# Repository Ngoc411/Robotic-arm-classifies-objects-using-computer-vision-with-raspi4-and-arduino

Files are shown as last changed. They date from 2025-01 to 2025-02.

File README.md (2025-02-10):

# Robotic-arm-classifies-objects-using-computer-vision-with-raspi4-and-arduino

## Description

This project involves a robotic arm capable of classifying objects using computer vision and sorting them accordingly. A Raspberry Pi 4 processes images captured from a camera, runs a trained machine learning model, and communicates with an Arduino to control the robotic arm’s movements.

<div align="center">
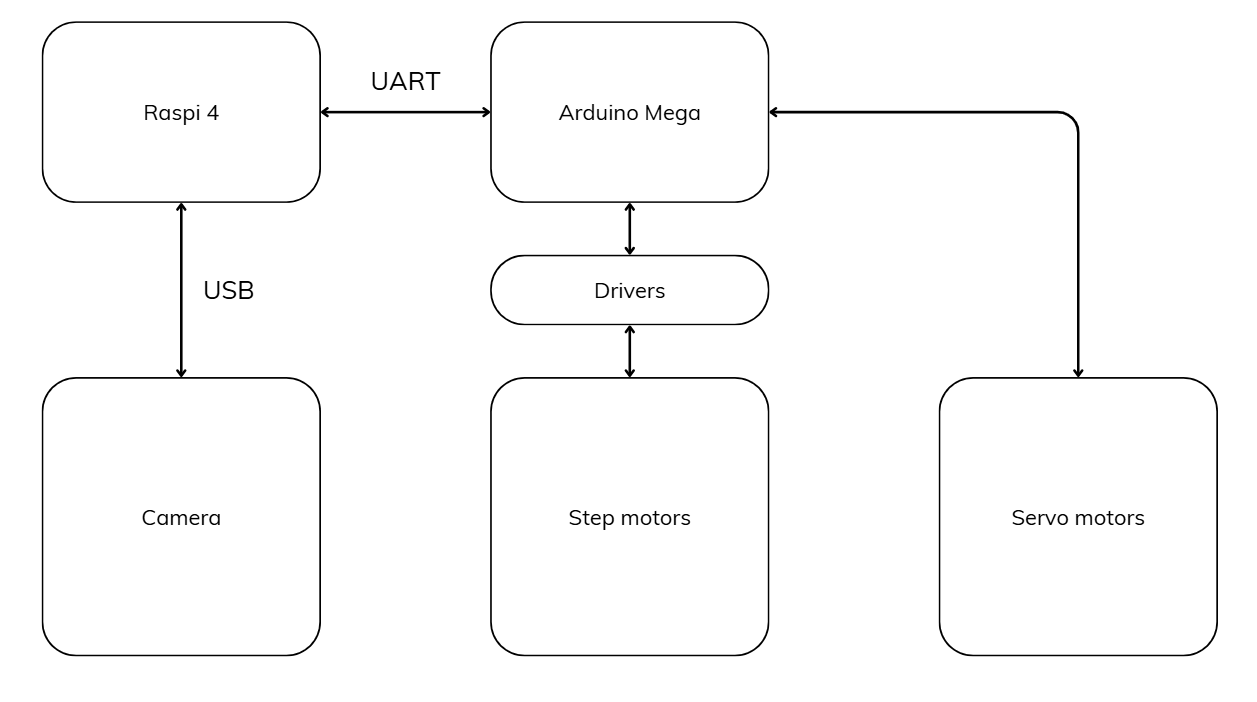
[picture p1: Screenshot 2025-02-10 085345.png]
  
</div>
<div align="center">
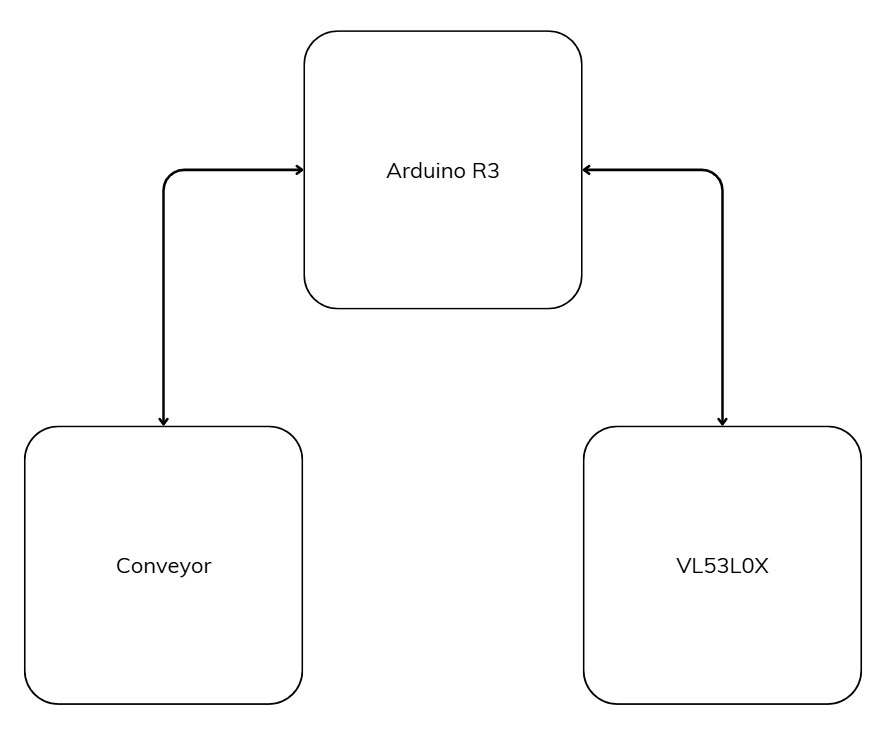
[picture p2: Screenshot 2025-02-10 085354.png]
  
</div>
<div align="center">
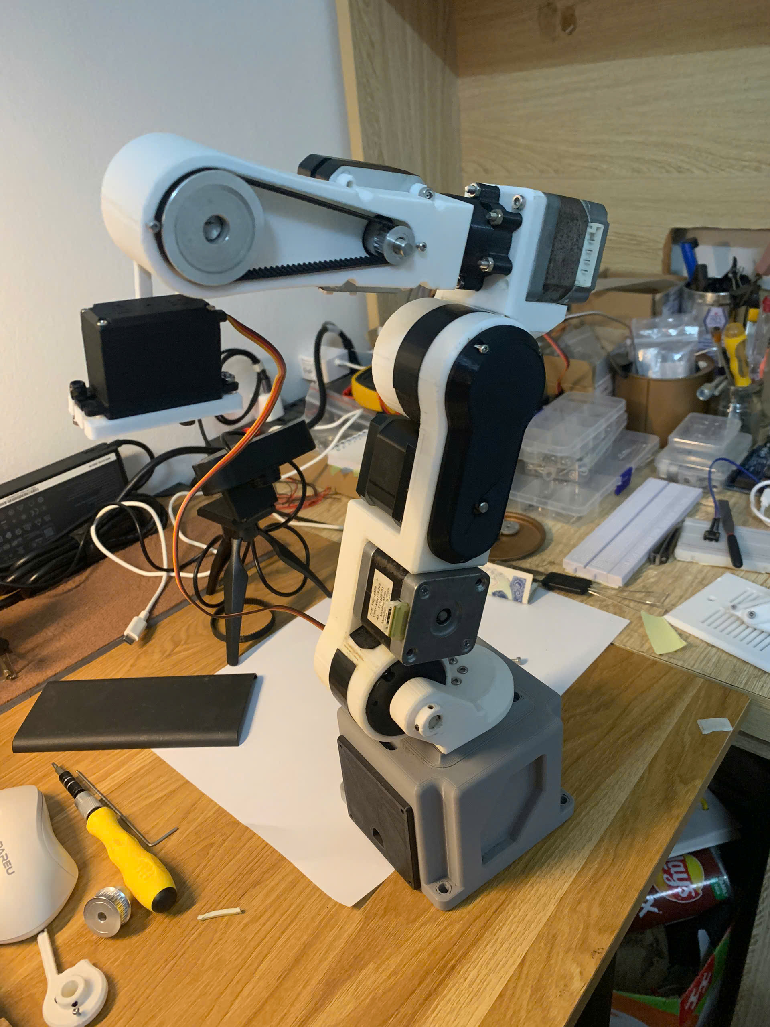
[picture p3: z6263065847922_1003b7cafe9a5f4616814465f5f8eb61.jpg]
  
</div>

## System Overview
1. Computer Vision Subsystem: Identifies and classifies objects

```mermaid
graph TD;
  A(Start) --> B(Initialize Camera & Load Model)
  B --> C(Capture Image)
  C --> D(Preprocess Image)
  D --> E(Run Object Classification Model)
  E -->|Success| F(Identify Object & Determine Target)
  E -->|Failure| C
  F --> G(Convert to Movement Commands)
  G --> H{received_data = True?}
  H -->|No| M{Exit?}
  H -->|Yes| I(Send Command to Arduino)
  I --> J(Set received_data = False)
  J --> K{Wait for Acknowledgment?}
  K -->|No| M
  K -->|Yes| L(Set received_data = True)
  M -->|No| C
  M -->|Yes| N(End)
```
  
2. Robotic Control Subsystem: Moves the robotic arm based on classifications.

``` mermaid
graph TD;
  A(Start) --> B(Initialize Serial Communication & Motors)
  B --> C{Wait for Command?}
  C -->|No| C
  C -->|Yes| D(Decode Received Command)
  D --> E(Convert to Joint Angles)
  E --> F{Are Angles Valid?}
  F -->|No| G(Send Error & Return to Wait)
  F -->|Yes| H(Move Servos)
  H --> I{Movement Complete?}
  I -->|No| H
  I -->|Yes| J(Send Acknowledgment to Raspberry Pi)
  J --> K{Exit?}
  K -->|Yes| C
  K -->|No| L(End)
```

## Hardware Components

- Raspberry Pi 4: Runs object classification and sends movement commands.
- Arduino: Controls the robotic arm servos.
- Camera Module: Captures images for object recognition.
- Robotic Arm with Step Motors and Servo Motors: Moves objects based on classification.
- Drivers: 8825
- Power Supply: 24V 5A Provides power to components.
- Arm design
<div align="center">
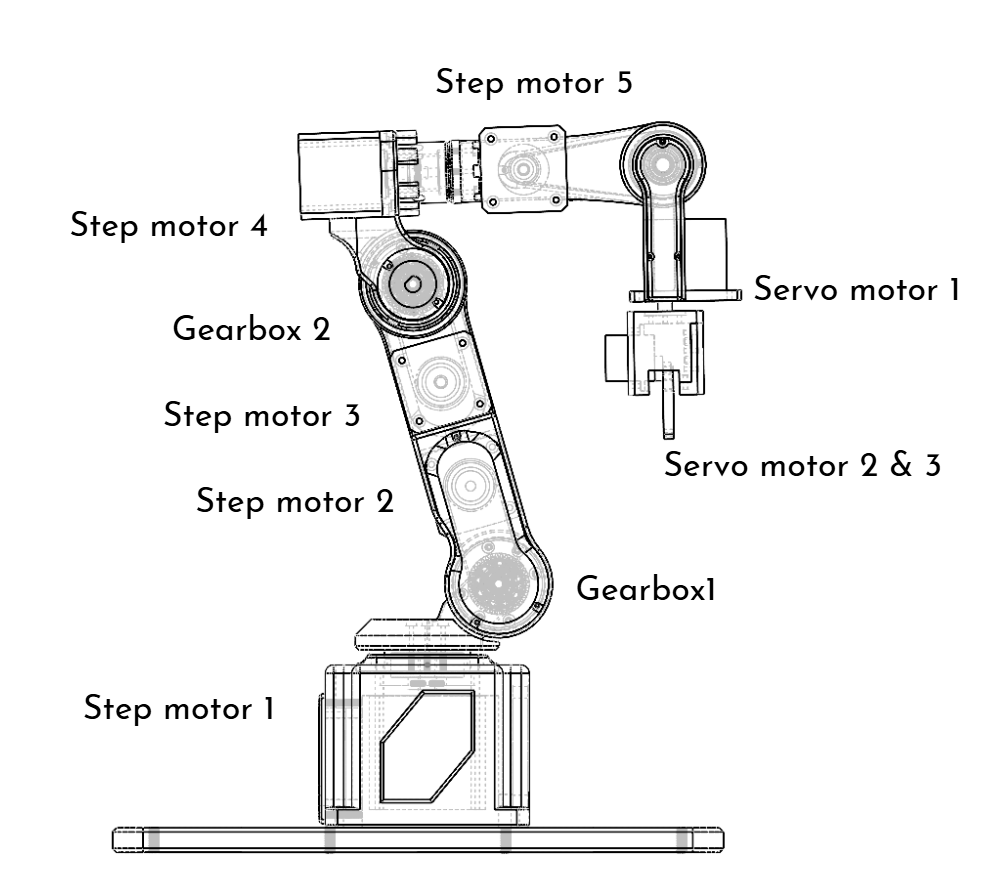
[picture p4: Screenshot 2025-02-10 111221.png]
  
</div>

## Model Training Process

1. Data Collection: Capture images of objects using the camera module.
<div align="center"; display="flex">
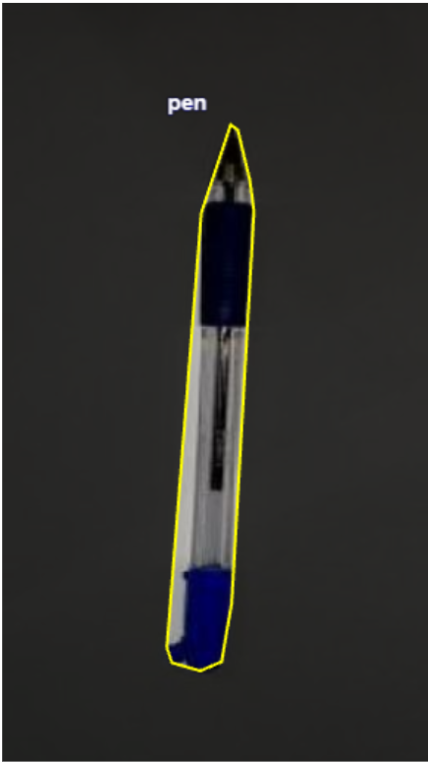
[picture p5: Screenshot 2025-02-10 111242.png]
  
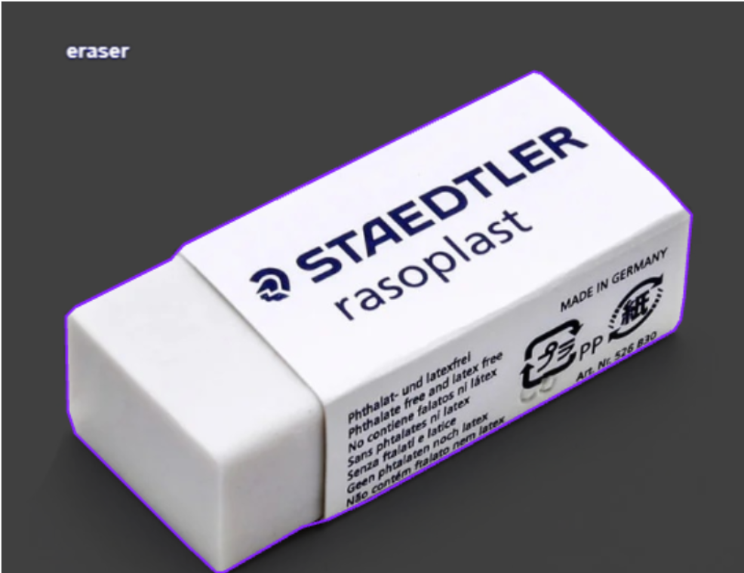
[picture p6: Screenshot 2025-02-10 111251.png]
  
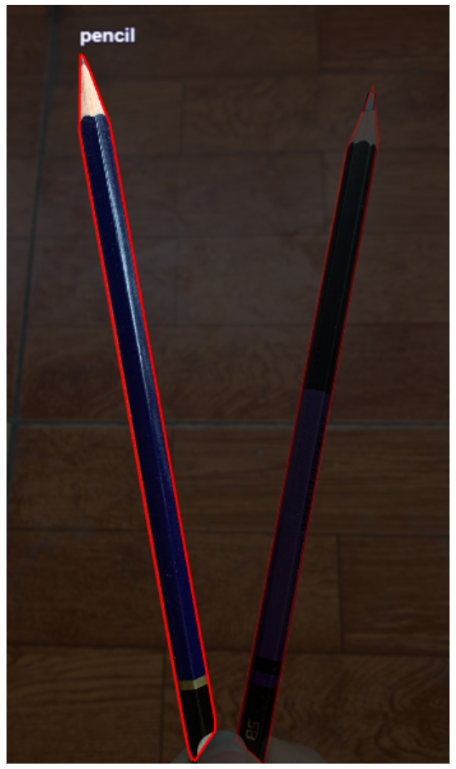
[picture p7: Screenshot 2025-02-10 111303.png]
  
</div>
2. Preprocessing: Resize, normalize, and augment images.

<div align="center">
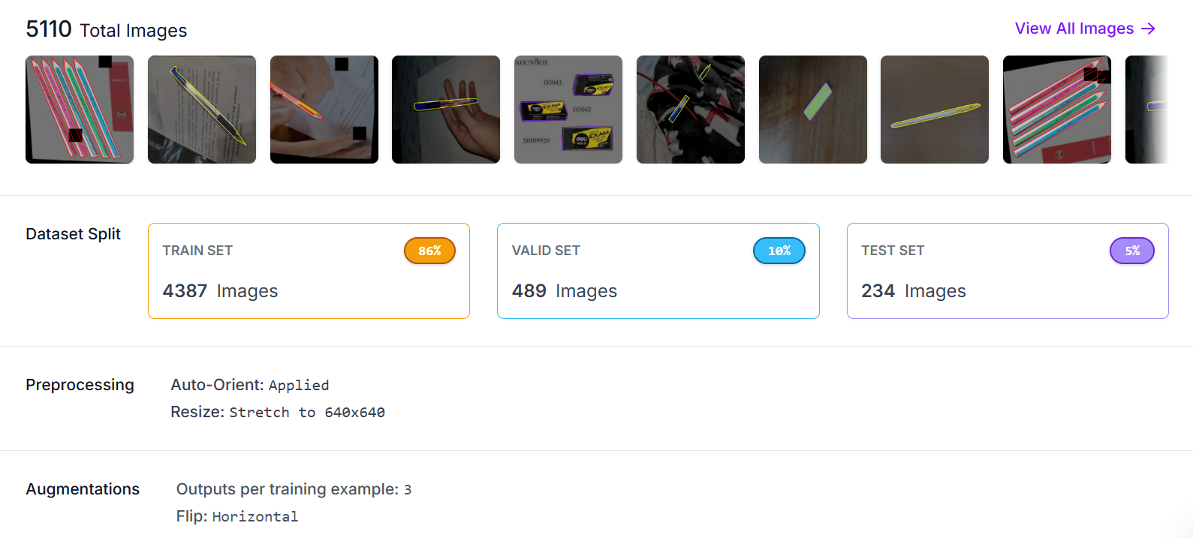
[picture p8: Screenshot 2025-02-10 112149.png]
  
</div>

3. Model Selection: Use a convolutional neural network (CNN) for classification.
4. Training: Train the model using TensorFlow/Keras.

<div align="center"; display="flex">
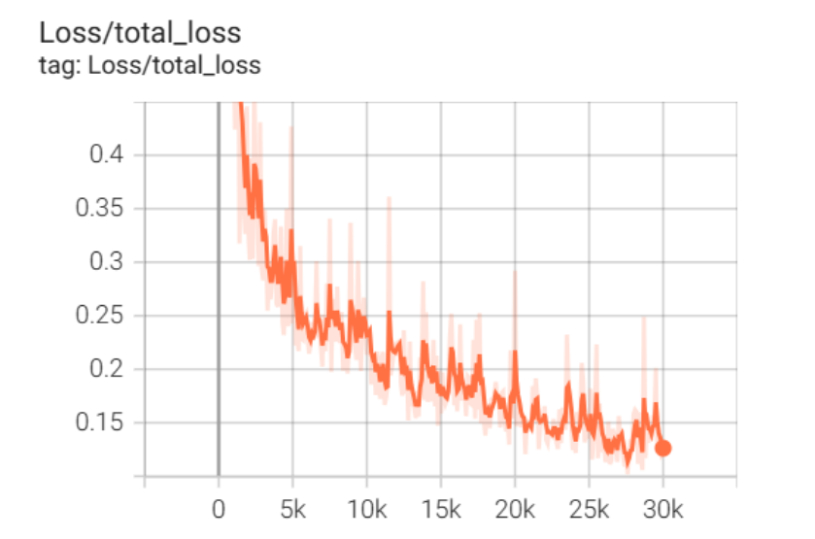
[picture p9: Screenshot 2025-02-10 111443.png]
  
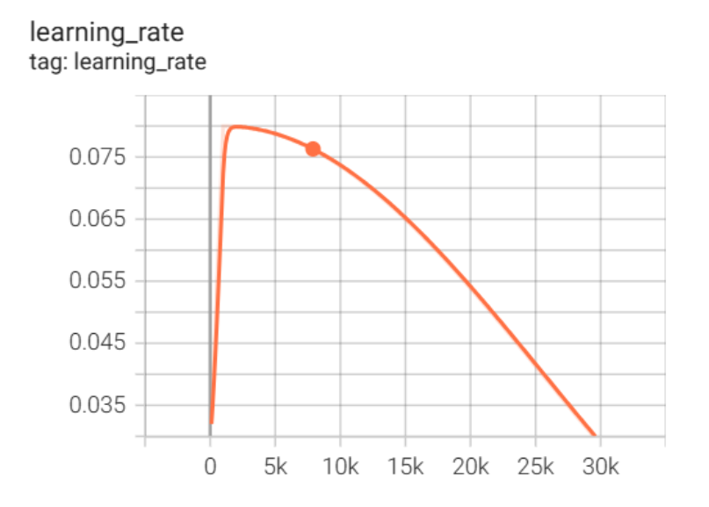
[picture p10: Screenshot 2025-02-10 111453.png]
  
</div>

5. Deployment: Convert the trained model to a format suitable for Raspberry Pi.

## Robotic Arm Kinematics

<div align="center">
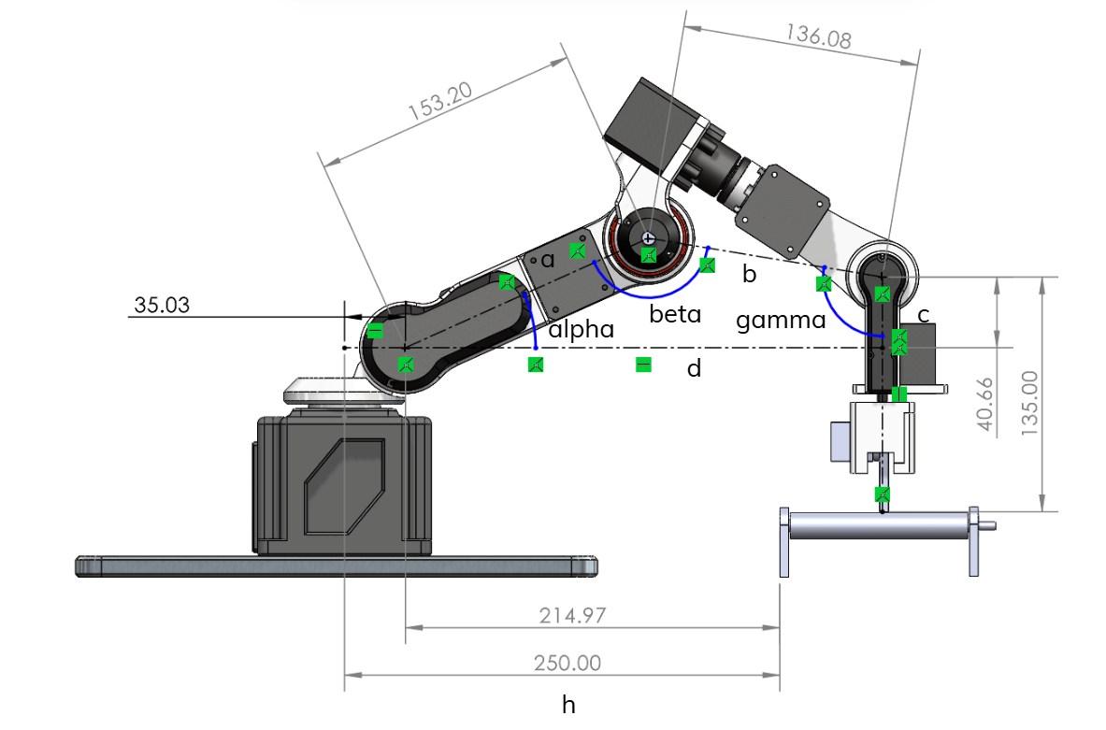
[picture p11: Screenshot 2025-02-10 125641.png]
  
</div>

The problem is to find 3 main angles: alpha, beta and gamma with fixed length a, b, c and h

<div align="center">
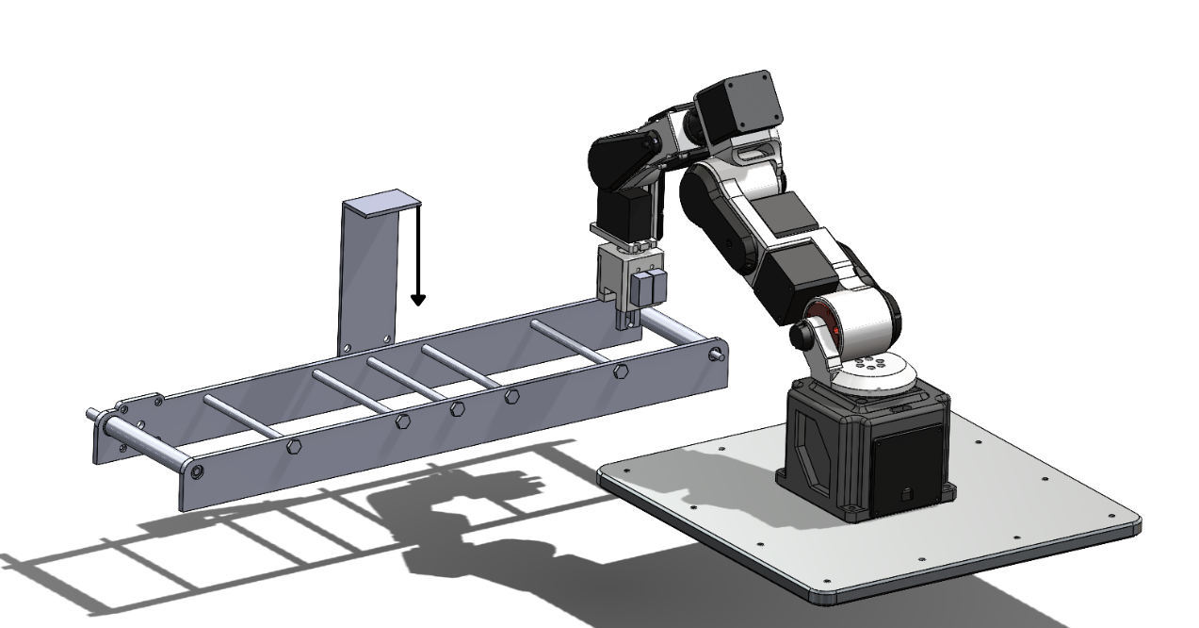
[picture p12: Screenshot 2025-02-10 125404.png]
  
</div>

The camera will be up side down like this, so we can base on the following picture to measure the coordinate of objects

<div align="center">
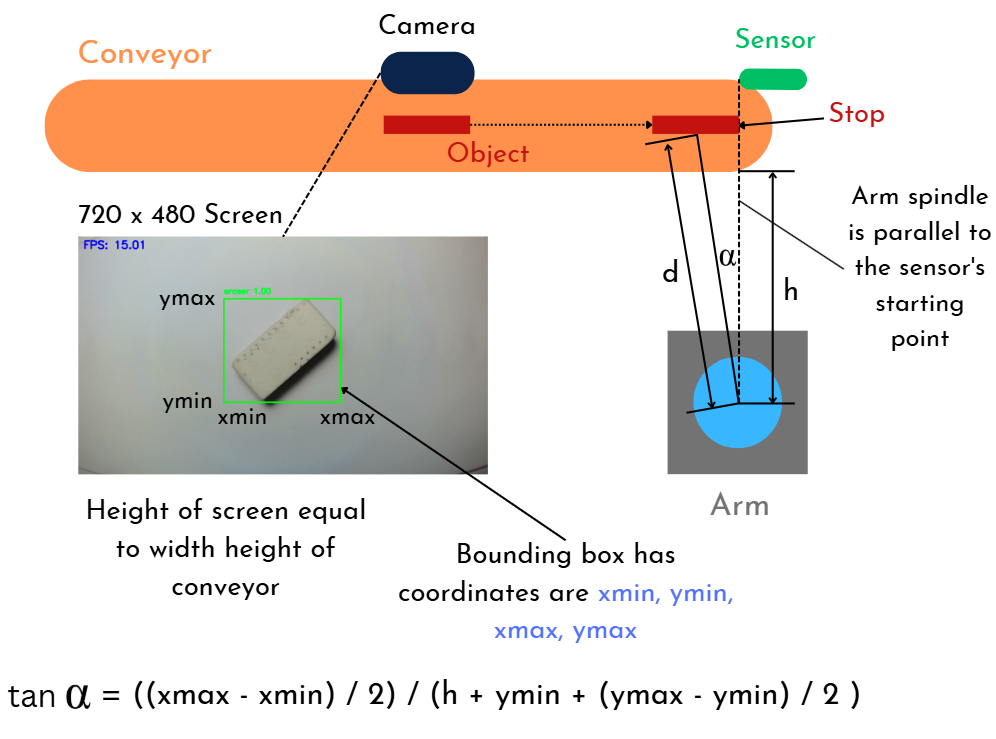
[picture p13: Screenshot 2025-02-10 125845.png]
  
</div>

## Operation

1. System Initialization: Start Raspberry Pi and Arduino.
2. Object Detection: Capture image and classify the object.

<div align="center">
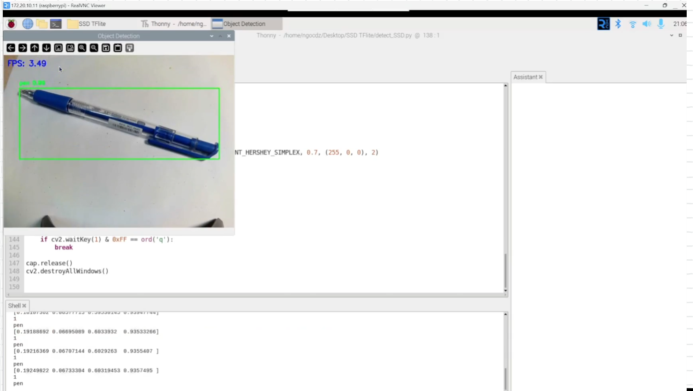
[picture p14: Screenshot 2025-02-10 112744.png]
  
</div>
<div align="center">
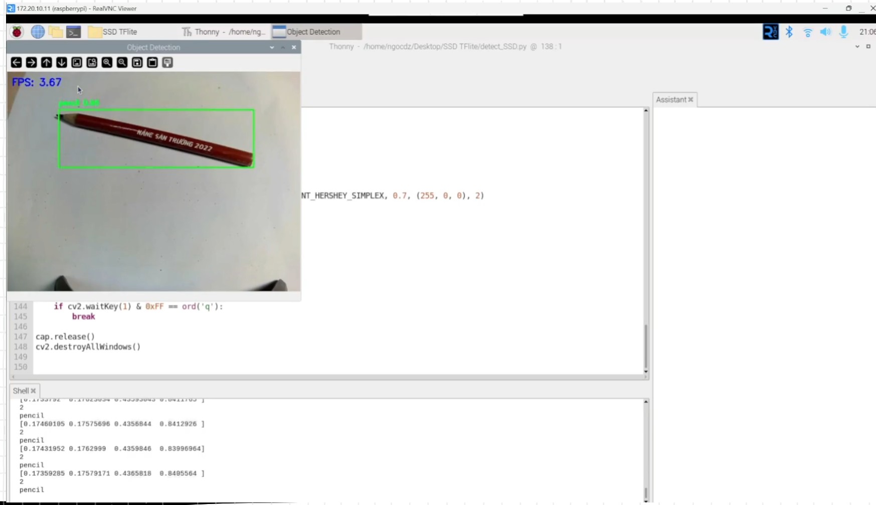
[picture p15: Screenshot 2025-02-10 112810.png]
  
</div>
<div align="center">
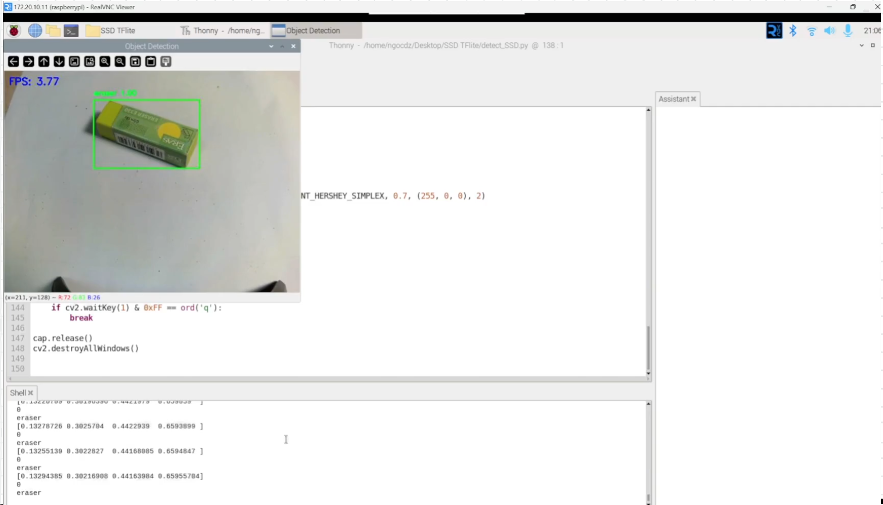
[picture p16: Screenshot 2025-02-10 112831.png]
  
</div>

3. Robotic Arm Movement: Calculate and execute joint angles for object handling.

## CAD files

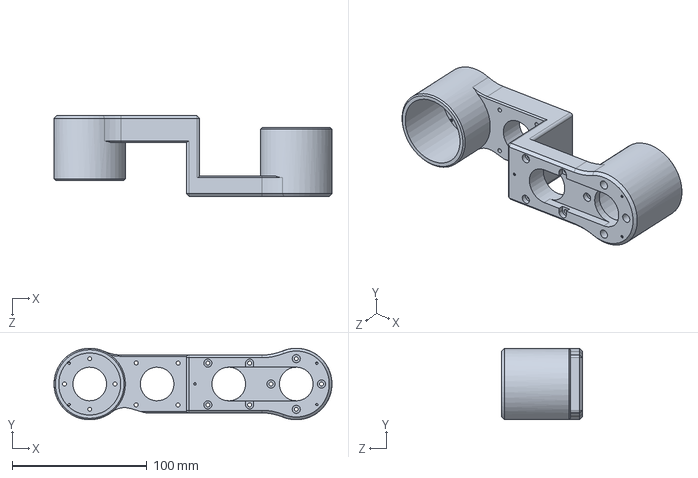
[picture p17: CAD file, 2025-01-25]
SolidW/Arm/Main Arm 1.SLDPRT
206.2 x 53.0 x 60.0 mm

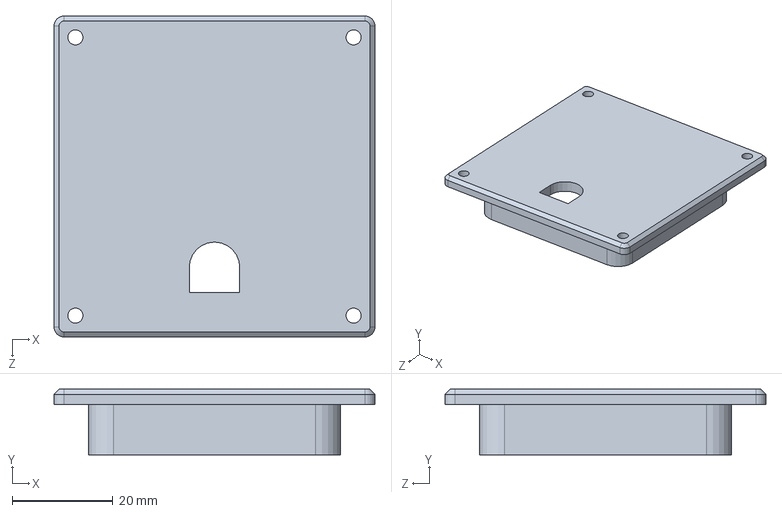
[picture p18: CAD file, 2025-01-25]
SolidW/Case/Part6 - Case.SLDPRT
63.6 x 13.0 x 63.6 mm

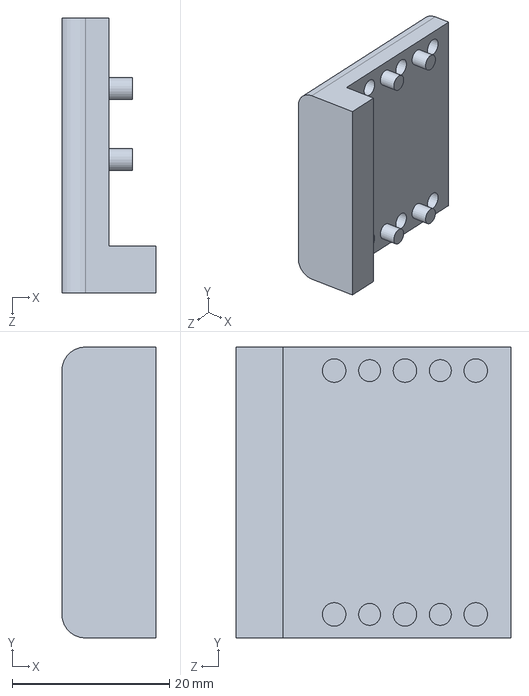
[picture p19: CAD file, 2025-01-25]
SolidW/Hand/Hand - 2.SLDPRT
12.0 x 37.0 x 35.0 mm

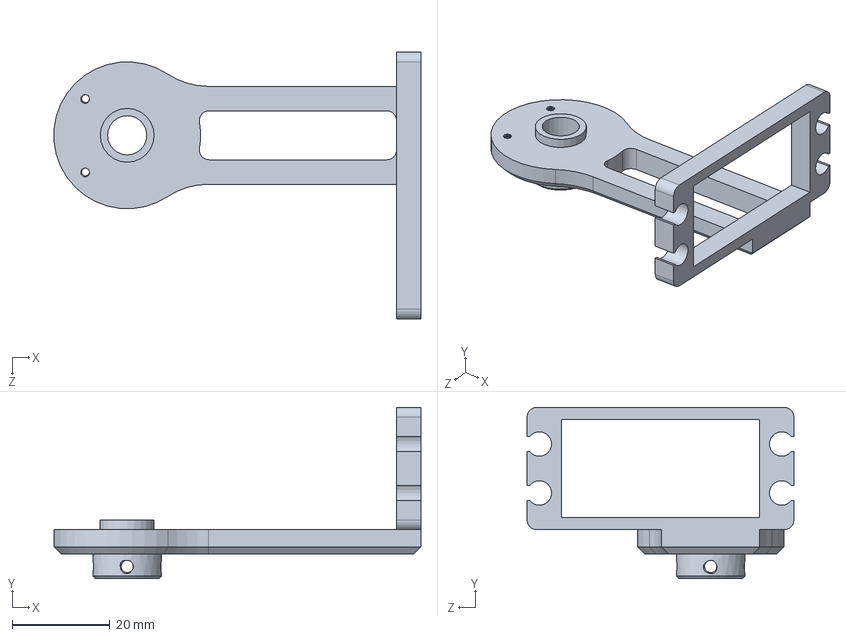
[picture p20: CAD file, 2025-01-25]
SolidW/Arm/Mini Arm.SLDPRT
74.9 x 35.0 x 54.5 mm

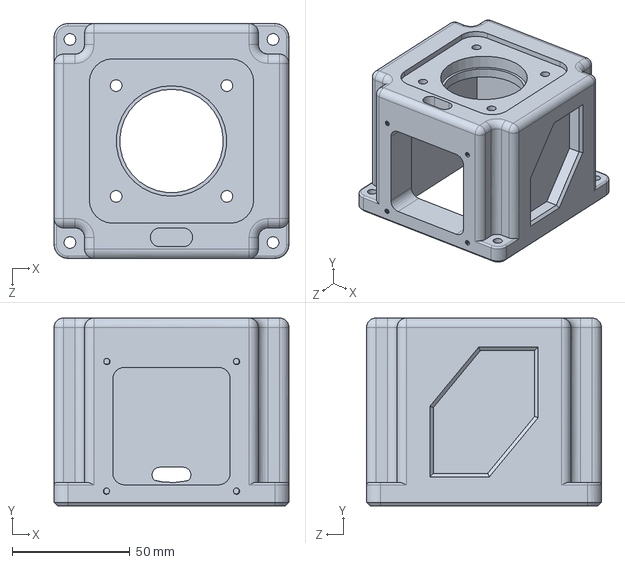
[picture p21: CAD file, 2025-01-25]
SolidW/Base/Base Case.SLDPRT
100.0 x 80.0 x 100.0 mm

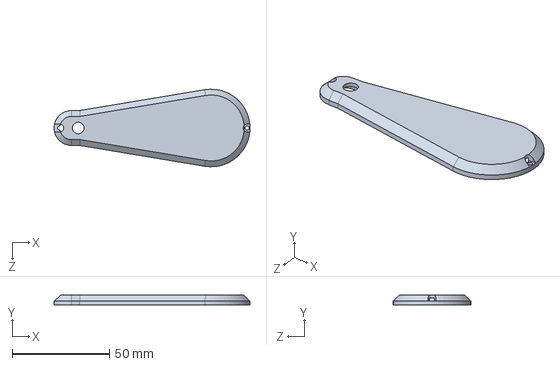
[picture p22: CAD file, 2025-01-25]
SolidW/Case/Part2 - Case.SLDPRT
101.0 x 5.00 x 40.0 mm

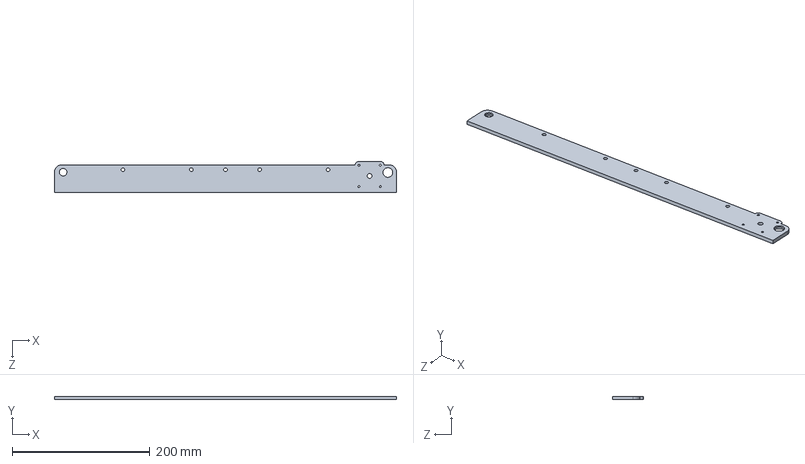
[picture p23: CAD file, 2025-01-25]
SolidW/Conveyor/Part2.SLDPRT
496.0 x 5.00 x 45.0 mm

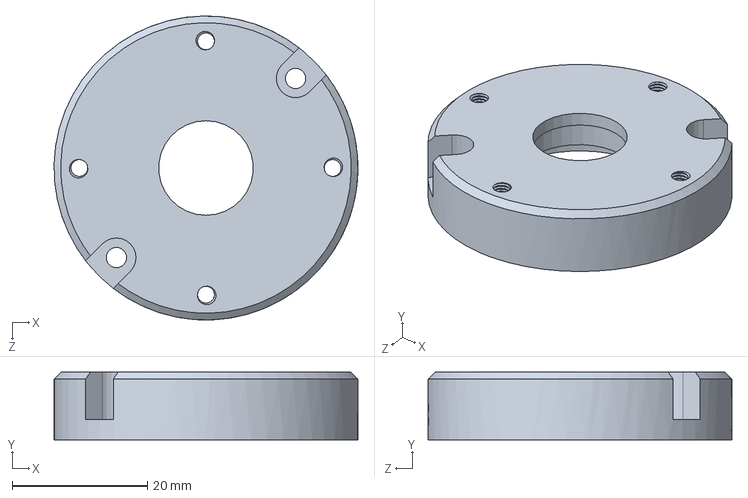
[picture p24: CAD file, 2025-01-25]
SolidW/Gearbox/Case Top.SLDPRT
45.0 x 10.0 x 45.0 mm

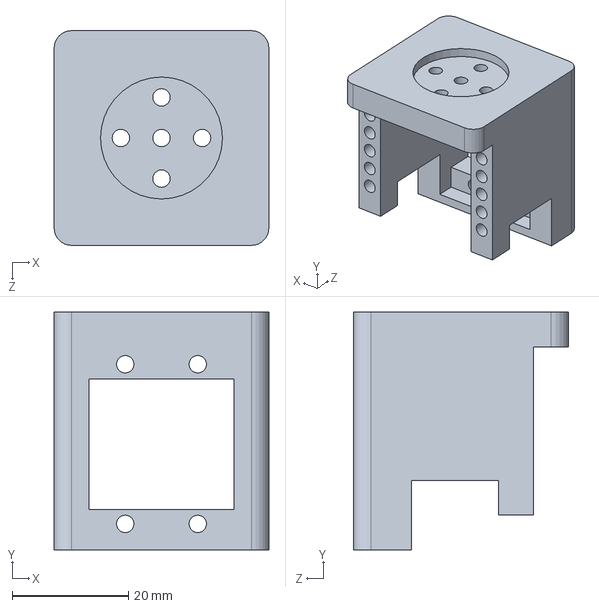
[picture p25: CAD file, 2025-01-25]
SolidW/Hand/Hand - 1.SLDPRT
37.0 x 41.0 x 37.0 mm

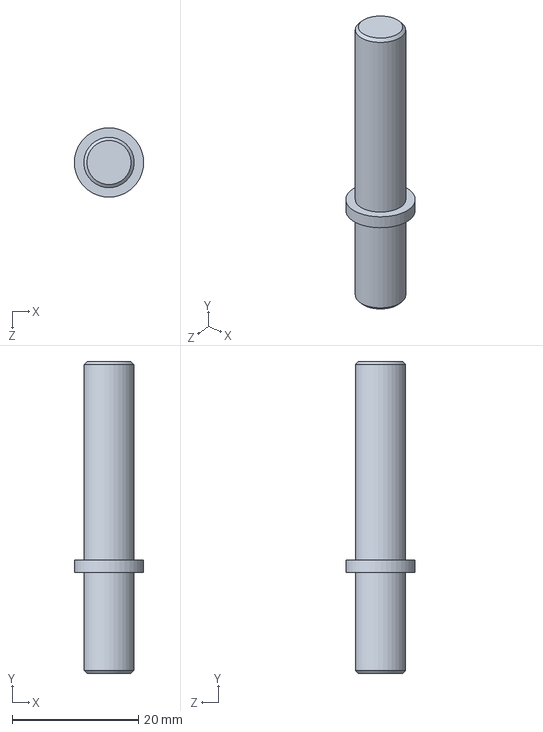
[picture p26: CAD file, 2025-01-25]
SolidW/Arm/Bar Connection Extra Arm 1.SLDPRT
11.0 x 49.5 x 11.0 mm

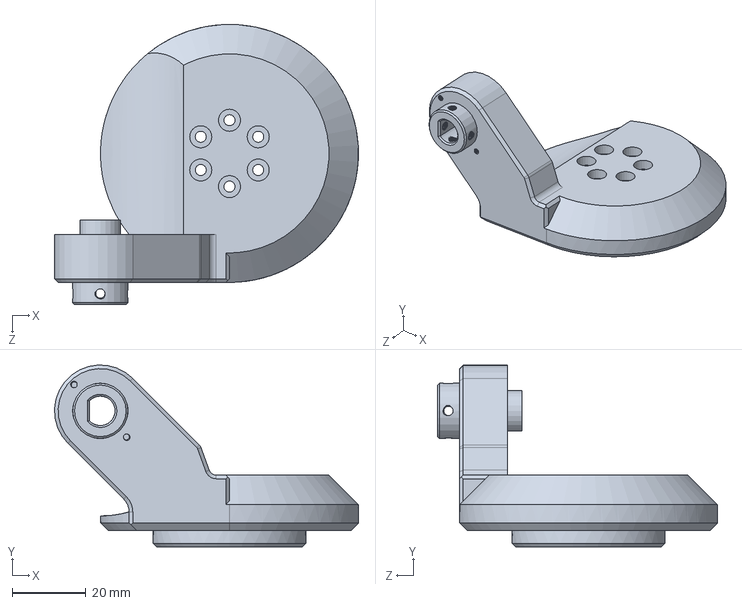
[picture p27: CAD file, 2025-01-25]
SolidW/Base/Base Connection 2.SLDPRT
82.5 x 49.4 x 76.0 mm

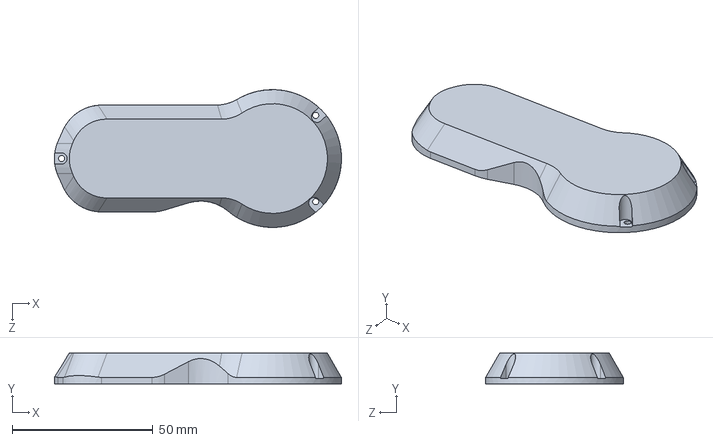
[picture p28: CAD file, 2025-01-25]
SolidW/Case/Part3 - Case.SLDPRT
102.0 x 11.0 x 49.0 mm

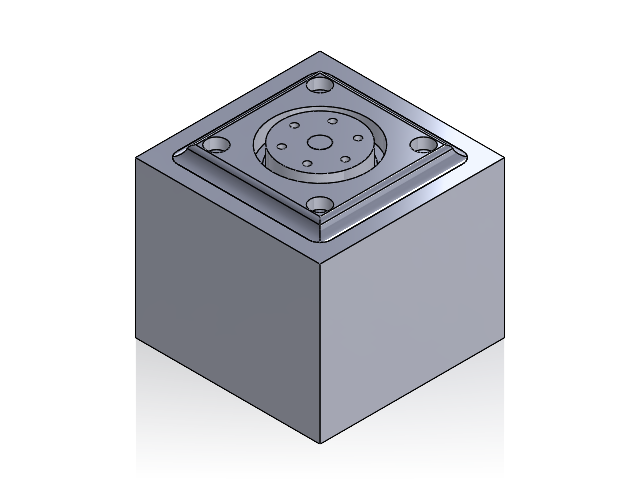
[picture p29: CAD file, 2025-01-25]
SolidW/Base/Assem Base.SLDASM
Base Case
Step Motor 57
Base Connection
Bearing 35x47x7
Bearing Block

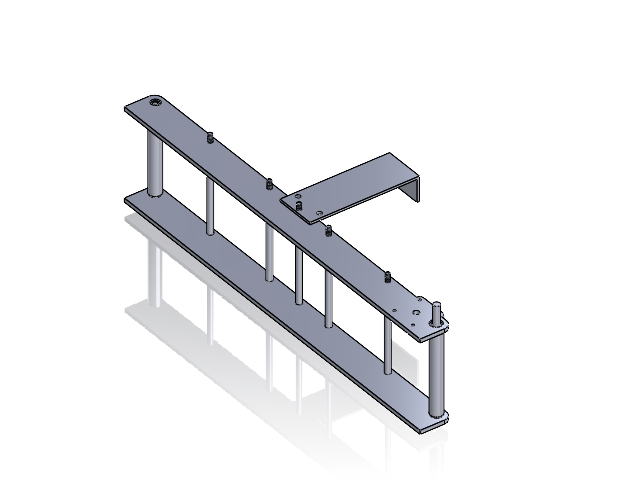
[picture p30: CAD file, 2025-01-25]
SolidW/Conveyor/Assem Conveyor.SLDASM
Bearing 5x13x4 x 3
Bearing 8x16x4

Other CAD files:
SolidW/Gearbox/Assem test gear 3.SLDASM
SolidW/Gearbox/Assem test gear 2.SLDASM
SolidW/Gearbox/Assem test gear.SLDASM
SolidW/Gearbox/Assem Gear.SLDASM
SolidW/Arm/Arm Connection 2.SLDPRT
SolidW/Arm/Arm Connection.SLDPRT
SolidW/Arm/Bar Connection Extra Arm 2.SLDPRT
SolidW/Arm/Extra Arm 2.SLDPRT
SolidW/Base/Base Connection.SLDPRT
SolidW/Base/Bearing Block.SLDPRT
SolidW/Case/Part1 - Case.SLDPRT
SolidW/Case/Part4 - Case.SLDPRT
SolidW/Case/Part5 - Case.SLDPRT
SolidW/Case/Part7 - Case.SLDPRT
SolidW/Conveyor/Bar Connection.SLDPRT
SolidW/Conveyor/Part1.SLDPRT
SolidW/Conveyor/Part3.SLDPRT
SolidW/Conveyor/Part4.SLDPRT
SolidW/Conveyor/Part5.SLDPRT
SolidW/Conveyor/Part6.SLDPRT
SolidW/Gearbox/Case Bottom.SLDPRT
SolidW/Gearbox/Gear 12 - 2.SLDPRT
SolidW/Gearbox/Gear 12 - 20.SLDPRT
SolidW/Gearbox/Gear 36 Internal - 20.SLDPRT
SolidW/Gearbox/Gear12 Start.SLDPRT
SolidW/Gearbox/Gear12.SLDPRT
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

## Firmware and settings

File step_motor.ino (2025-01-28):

#include <stdio.h>
#include <math.h> 
#include <Wire.h>
#include <Servo.h>
#include <AccelStepper.h>

#define bigServoPin 2
#define rightSmallServoPin 3
#define leftSmallServoPin 4

#define enPin42 5

#define dirPin42_1 6
#define stepPin42_1 7
#define SPR42_1 400

#define dirPin42_2 8
#define stepPin42_2 9
#define SPR42_2 400

#define dirPin42_3 10
#define stepPin42_3 11
#define SPR42_3 400

#define dirPin42_4 12
#define stepPin42_4 13
#define SPR42_4 400

#define dirPin57 14
#define stepPin57 15
#define SPR57 800

Servo bigServo;
Servo rightSmallServo;
Servo leftSmallServo;

AccelStepper stepper42_1(1, stepPin42_1, dirPin42_1);
AccelStepper stepper42_2(1, stepPin42_2, dirPin42_2);
AccelStepper stepper42_3(1, stepPin42_3, dirPin42_3);
AccelStepper stepper42_4(1, stepPin42_4, dirPin42_4);
AccelStepper stepper57(1, stepPin57, dirPin57);

float a = 153.2;
float b = 136.08;
float c = 41.17;
int h = 250;

float alpha = 0.0;
float beta = 0.0;
float gamma = 0.0;

bool ready = false;
bool homeReady = true;

#define DATA_SIZE 6

uint8_t current_data[DATA_SIZE] = {0};  
bool received_data = false;  


// --------------------------------------------------------------------------------------------------------------------------------------------------------

void setup() {
  Serial.begin(115200);

  bigServo.attach(bigServoPin);
  bigServo.write(90);
  rightSmallServo.attach(rightSmallServoPin);
  leftSmallServo.attach(leftSmallServoPin);

  pinMode(dirPin42_1, OUTPUT);
  pinMode(stepPin42_1, OUTPUT);
  pinMode(dirPin42_2, OUTPUT);
  pinMode(stepPin42_2, OUTPUT);
  pinMode(dirPin42_3, OUTPUT);
  pinMode(stepPin42_3, OUTPUT);
  pinMode(dirPin42_4, OUTPUT);
  pinMode(stepPin42_4, OUTPUT);
  pinMode(dirPin57, OUTPUT);
  pinMode(stepPin57, OUTPUT);

  pinMode(enPin42, OUTPUT);


  digitalWrite(enPin42, LOW); // Kích hoạt động cơ 2

  stepper42_1.setMaxSpeed(20000); 
  stepper42_1.setAcceleration(4000);
  // stepper42_1.setSpeed(300); // Tốc độ ban đầu cho động cơ 1

  stepper42_2.setMaxSpeed(20000); 
  stepper42_2.setAcceleration(4000);
  // stepper42_2.setSpeed(500); // Tốc độ ban đầu cho động cơ 2

  stepper42_3.setMaxSpeed(20000); 
  stepper42_3.setAcceleration(4000);
  // stepper42_3.setSpeed(700); // Tốc độ ban đầu cho động cơ 3

  stepper42_4.setMaxSpeed(20000); 
  stepper42_4.setAcceleration(4000);
  // stepper42_4.setSpeed(900); // Tốc độ ban đầu cho động cơ 4

  stepper57.setMaxSpeed(30000); 
  stepper57.setAcceleration(8000);
}

void loop() {
  receiveUARTData();

  if(!homeReady) {
    home(-2482, -2868, 0, 280, 0, 90, 90, 90);
  }
  if (received_data) {
    unitArm();
    received_data = false;
  }
}

// --------------------------------------------------------------------------------------------------------------------------------------------------------

// -------------------- //

void actPhase(
  int deg42_1_grip,
  int deg42_2_grip, 
  int deg42_3_grip, 
  int deg42_4_grip,
  int degServo_obj,
  int deg57_obj,
  int deg57_class
) { // thực hiện nhiệm vụ gắp và phân loại

  // bước 1: di chuyển cánh tay để gắp vặt thể
  spinObjDeg(90 - degServo_obj + deg57_obj);
  rightSmallServo.write(0); 
  leftSmallServo.write(180); 
  
  stepper42_1.moveTo(deg42_1_grip); // come to grip object
  stepper42_2.moveTo(deg42_2_grip); 
  stepper42_3.moveTo(deg42_3_grip); 
  stepper42_4.moveTo(deg42_4_grip); 
  stepper57.moveTo(deg57_obj);
  while (stepper42_1.distanceToGo() || stepper42_2.distanceToGo() || stepper42_3.distanceToGo() || stepper42_4.distanceToGo() || stepper57.distanceToGo()) {
    stepper42_1.run(); // Chạy động cơ 1
    stepper42_2.run(); // Chạy động cơ 2
    stepper42_3.run(); // Chạy động cơ 3
    stepper42_4.run(); // Chạy động cơ 4
    stepper57.run(); // Chạy động cơ 57
  }
  stepper42_1.setCurrentPosition(0);
  stepper42_2.setCurrentPosition(0);
  stepper42_3.setCurrentPosition(0);
  stepper42_4.setCurrentPosition(0);
  stepper57.setCurrentPosition(0);

  delay(500);

  // bước 2: gắp vật thể
  grip();

  delay(1000);

  // bước 3: chuyển cánh tay đến vùng phân loại
  stepper42_1.moveTo(deg42_1_grip - 1860); 
  stepper42_2.moveTo(-1086 - deg42_2_grip); 
  stepper42_3.moveTo(0); 
  stepper42_4.moveTo(-90 - deg42_4_grip); 
  stepper57.moveTo(deg57_class - deg57_obj); 
  while (stepper42_1.distanceToGo() || stepper42_2.distanceToGo() || stepper42_3.distanceToGo() || stepper42_4.distanceToGo() || stepper57.distanceToGo()) {
    stepper42_1.run(); // Chạy động cơ 1
    stepper42_2.run(); // Chạy động cơ 2
    stepper42_3.run(); // Chạy động cơ 3
    stepper42_4.run(); // Chạy động cơ 4
    stepper57.run(); // Chạy động cơ 57
  }
  stepper42_1.setCurrentPosition(0);
  stepper42_2.setCurrentPosition(0);
  stepper42_3.setCurrentPosition(0);
  stepper42_4.setCurrentPosition(0);
  stepper57.setCurrentPosition(0);

  delay(1000);

  // bước 4: thả vật thể
  drop();

  delay(1000);

  // bước 5: chuyển hình dạng cánh tay về dạng mặc định 

  home(1860, 1086, 0, 90, -deg57_class, 90, 90, 90);

  Serial.write(0x01);
}

void home(int degHome42_1, int degHome42_2, int degHome42_3, int degHome42_4, int degHome57, int degHomeBigSer, int degHomeRightSmallSer, int degHomeLeftSmallSer) {
  spinObjDeg(degHomeBigSer);
  rightSmallServo.write(degHomeRightSmallSer); 
  leftSmallServo.write(degHomeLeftSmallSer); 

  stepper42_1.moveTo(degHome42_1); // turn back the arm to home position
  stepper42_2.moveTo(degHome42_2); 
  stepper42_3.moveTo(degHome42_3); 
  stepper42_4.moveTo(degHome42_4); 
  stepper57.moveTo(degHome57); 
  while (stepper42_1.distanceToGo() || stepper42_2.distanceToGo() || stepper42_3.distanceToGo() || stepper42_4.distanceToGo() || stepper57.distanceToGo()) {
    stepper42_1.run(); // Chạy động cơ 1
    stepper42_2.run(); // Chạy động cơ 2
    stepper42_3.run(); // Chạy động cơ 3
    stepper42_4.run(); // Chạy động cơ 4
    stepper57.run(); // Chạy động cơ 57
  }
  stepper42_1.setCurrentPosition(0);
  stepper42_2.setCurrentPosition(0);
  stepper42_3.setCurrentPosition(0);
  stepper42_4.setCurrentPosition(0);
  stepper57.setCurrentPosition(0);

  homeReady = true;
}

// -------------------- //

void spinObjDeg(int deg_obj) {
  bigServo.write(deg_obj);
}

// -------------------- //

void grip() { // gắp vật thể
  rightSmallServo.write(90); 
  leftSmallServo.write(90); 
  Serial.write("Done");
}

// -------------------- //

void drop() { // thả vật thể
  rightSmallServo.write(0); 
  leftSmallServo.write(90); 
}

// -------------------- //

void unitArm() {
    if (ready){
      stepper42_1_deg(a, b, c, cal_d(current_data, h, stepper57_deg(current_data, h)), cal_e(c, cal_d(current_data, h, stepper57_deg(current_data, h))));
      stepper42_2_deg(a, b, c, cal_d(current_data, h, stepper57_deg(current_data, h)), cal_e(c, cal_d(current_data, h, stepper57_deg(current_data, h))));
      stepper42_4_deg(alpha, beta);

      actPhase(
        convert_deg_to_phase(42, 27, alpha),
        convert_deg_to_phase(42, 27, beta),
        0,
        convert_deg_to_phase(42, 3, gamma),
        (int)(current_data[5]),
        convert_deg_to_phase(57, 1, stepper57_deg(current_data, h)),
        convert_deg_to_phase(57, 1, cal_deg_57_class(current_data))
      );
    }
}

// -------------------- //

void receiveUARTData() {
  if (Serial.available() >= DATA_SIZE) 
    for (int i = 0; i < DATA_SIZE; i++) {
      current_data[i] = Serial.read();
    }
    received_data = true;
  }
}

// -------------------- //

int convert_from_pixel_to_mm(int pixel) {
  return (5 * pixel) / 24;  
}

float stepper57_deg(uint8_t current_data[6], int h) {
  int ymin = (int)current_data[0];
  int xmin = current_data[1];
  int ymax = current_data[2];
  int xmax = current_data[3];

  float deg_57 = round(atan(((xmax - xmin) / 2.0) / (h + ymin + (ymax - ymin) / 2.0)) * (180.0 / M_PI) * 1000.0) / 1000.0;

  return deg_57; 
}

int cal_d(uint8_t current_data[6], int h, float deg_57) { 
  int ymin = current_data[0];
  int xmin = current_data[1];
  int ymax = current_data[2];
  int xmax = current_data[3];

  float deg_57_radians = deg_57 * (M_PI / 180.0);

  float sin_deg_57 = sin(deg_57_radians);

  if (sin_deg_57 == 0) {
      printf("Error: sin(alpha) is zero, cannot divide by zero.\n");
      return -1;
  }

  int d = (convert_from_pixel_to_mm(xmax) - convert_from_pixel_to_mm(xmin)) / 2 / sin_deg_57;

  return d; 
}

float cal_e(float c, int d) {
  float e = round(sqrt(pow(c, 2) + pow(d, 2)) * 1000.0) / 1000.0;
  return e;
}

void stepper42_1_deg(float a, float b, float c, int d, float e) {
  float alpha_1 = round(acos((pow(a, 2) + pow(e, 2) - pow(b, 2)) / (2 * a * e)) * 1000.0) / 1000.0;
  float alpha_2 = round(atan(c / d) * 1000.0) / 1000.0;

  alpha = (alpha_1 + alpha_2) - 90.0;
}
void stepper42_2_deg(float a, float b, float c, int d, float e) {
  beta = 113.61 - (round(acos((pow(a, 2) + pow(b, 2) - pow(e, 2)) / (2 * a * b)) * 1000.0) / 1000.0);
}
// float stepper42_3_deg(float a, float b, float c, int d, float e) {
// }
void stepper42_4_deg(float alpha, float beta) {
  gamma = 66.39 - (round(360.0 - 90.0 - alpha - beta) * 1000.0) / 1000.0;
}


float cal_deg_57_class(uint8_t current_data[6]) {
  uint8_t id = current_data[4];
  if(id == 0) {
    return -60.0;
  } if(id == 1) {
    return 60.0;
  } if(id == 2) {
    return 120.0;
  }
}


int convert_deg_to_phase(int type, int ratio, float deg) {
  if (type == 42) {
    return (int) ((deg * 400.0 * ratio) / 360.0);
  } 
  if (type == 57) {
    return (int) ((deg * 800.0 * ratio) / 360.0);
  }
  return 0; 
}

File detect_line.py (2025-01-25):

import cv2
import numpy as np
import math

def detect_line(frame):
    """
    Function to detect the longest line in a given frame using Canny edge detection
    and Hough Line Transformation.
    """
    max_len_line = 0
    max_len_line_index = None

    gray = cv2.cvtColor(frame, cv2.COLOR_BGR2GRAY)

    edges = cv2.Canny(gray, 50, 200, None, 3)

    linesP = cv2.HoughLinesP(edges, 1, np.pi / 180, 100, None, 60, 60)

    if linesP is not None:
        for i, lineP in enumerate(linesP):

            len_line = math.sqrt((lineP[0][2] - lineP[0][0])**2 + (lineP[0][3] - lineP[0][1])**2)

            if len_line > max_len_line:
                max_len_line = len_line
                max_len_line_index = i

            cv2.line(frame, (lineP[0][0], lineP[0][1]), (lineP[0][2], lineP[0][3]), (0, 0, 255), 3, cv2.LINE_AA)

        if max_len_line != 0 and max_len_line_index is not None:
            degree_theta = math.degrees(
                math.atan2(
                    linesP[max_len_line_index][0][3] - linesP[max_len_line_index][0][1],
                    linesP[max_len_line_index][0][2] - linesP[max_len_line_index][0][0]
                )
            )
            degree_theta = -degree_theta
            if degree_theta < 0:
                degree_theta = 180 + degree_theta
            if 178 <= degree_theta <= 180 or 0 <= degree_theta <= 2:
                degree_theta = 0

            print(f"Longest Line Angle: {degree_theta}°")

if __name__ == "__main__":
    cap = cv2.VideoCapture(1)  # Can swtich it to 0,2, ...
    cap.set(3, 640)  
    cap.set(4, 480)  

    while cap.isOpened():
        ret, frame = cap.read()
        if not ret:
            break

        detect_line(frame) 

        cv2.imshow('Line Detection', frame)

        if cv2.waitKey(1) & 0xFF == ord('q'):
            break

    cap.release()
    cv2.destroyAllWindows()
